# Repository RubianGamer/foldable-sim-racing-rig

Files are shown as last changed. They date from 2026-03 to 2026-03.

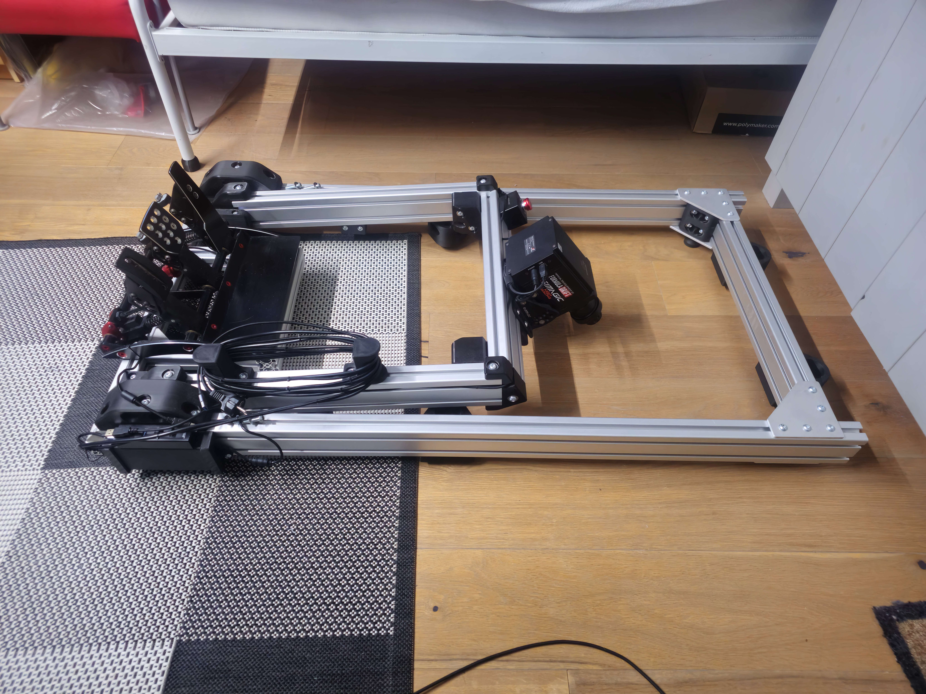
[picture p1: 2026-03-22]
images/20250122_214839.jpg

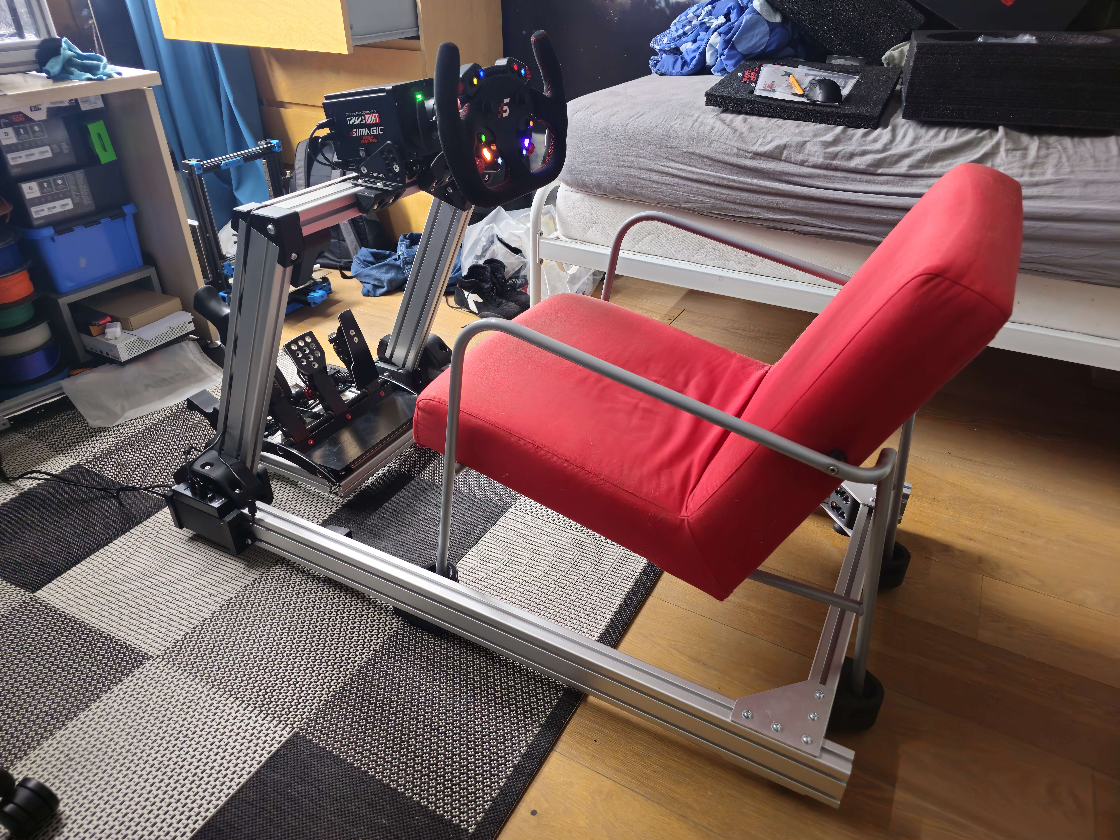
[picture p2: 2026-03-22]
images/20240603_111210.jpg

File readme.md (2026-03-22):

due to popular demand, here are the files for my folding sim rig/wheel stand.

was made to fit me (180cm tall, avg/slender build) with a random thrift shop seat set down in some mounts, so you will need to design your own seat mount or figure out what seat i used and find one somewhere lol (its a great chair)

my hardware is a simagic alpha mini with fanatec clubsport V3 pedals. the wheeldeck can prob support most deck mounted wheelbases, but the pedal deck is made specifically for the clubsport V3 pedals, so you might have to make something yourself if you use different pedal.

file comes with side braces, but after building it, i found out the deck as is can support my full weight (70kg) with practically no deflection even when moving around, so are not really needed.

some of the hardware might be difficult to source locally, especially the large washers and sholder bolts, but aliexpress has pretty much all of the hardware required. i got the brackets/plates/profiles off of aluxprofiel locally.

for the sholder bolts, the sholder is M12 (so 12mm), and the threads will be M10.

for the printed parts, print all the parts out of PLA/ASA with 3.2mm shell (8 perimiters and 16 top/bottom layers on .4 nozzle .2 layer height) and 50% infill for proper strenght, avoid PETG and ABS due to the material being less stiff. if you want absolutely no flex out of the printed parts you can always print with filled filaments, or with CF-PPS if you hate your wallet :)

render_front

render_front

render_front

render_front

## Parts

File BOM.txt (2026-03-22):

the parts you will need for the build. 

extrusion sizes:
490mm 8040  1x (wheel deck)
585mm 8040 2x (wheel deck stand)
700mm 4040 1x (front main frame)
1285mm 8040 2x (main frame sides)
620mm 8040 1x (rear main frame

only for fanatec clubsport V3 pedals:
208mm 4040 2x
325mm 4040 1x

screws:
M5x12 BHCS
M5x7mm heatset insert (8x) (9,5mm max lenght)

M8x60 BHCS
M8x30 BHCS
M8x20 BHCS
M8x16 BHCS
M8 hex nut
M8x20mm washer
M8 roll in nut for 40 series profile
rubber feet with M8 thread (see cad)

M12xx70mm sholder bolts (2x)
M12x25mm washer (2x)

M10 hex nut (2x)
M10x25x1,5mm washer (2x)

(ID,OD,lenght)
12x18x20 bronze bushing (6x)
12x18x12 bronze bushing (2x)

brackets:
4x 40 series L profile corner plates (2 need 10mm hole drilled)
2x square plate (4x2 holes, 40x80mm spacing, see cad)
4x 90 deg 40 series corner bracket (4x more for fanatec clubsport V3 pedal frame)

only for side braces:
245mm 4040 2x
M5x40 BHCS (8x)
M5 hex nut (8x)
M12x35mm sholder bolt (4x)
M10 hex nut (4x)
M10x25x1,5mm washer (4x)
M5x7mm heatset insert (16x) (9,5mm max lenght)

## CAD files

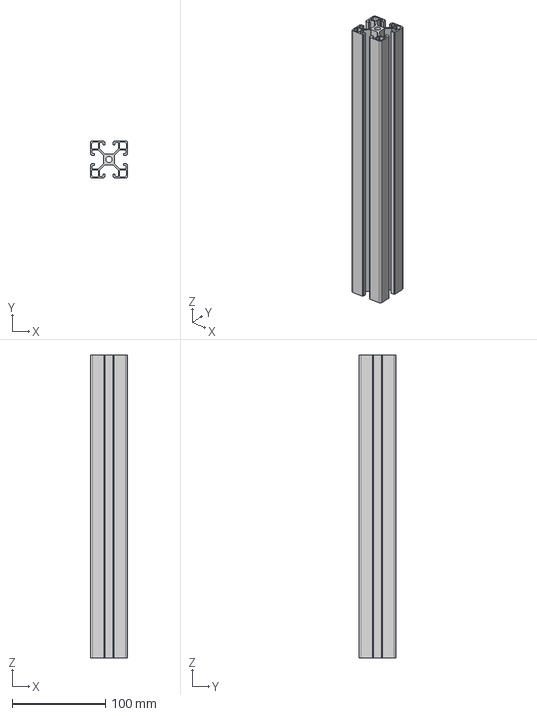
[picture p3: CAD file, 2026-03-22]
design files/step/aluminum profiles/fwd pedal mount v1.step
40.0 x 40.0 x 325.0 mm

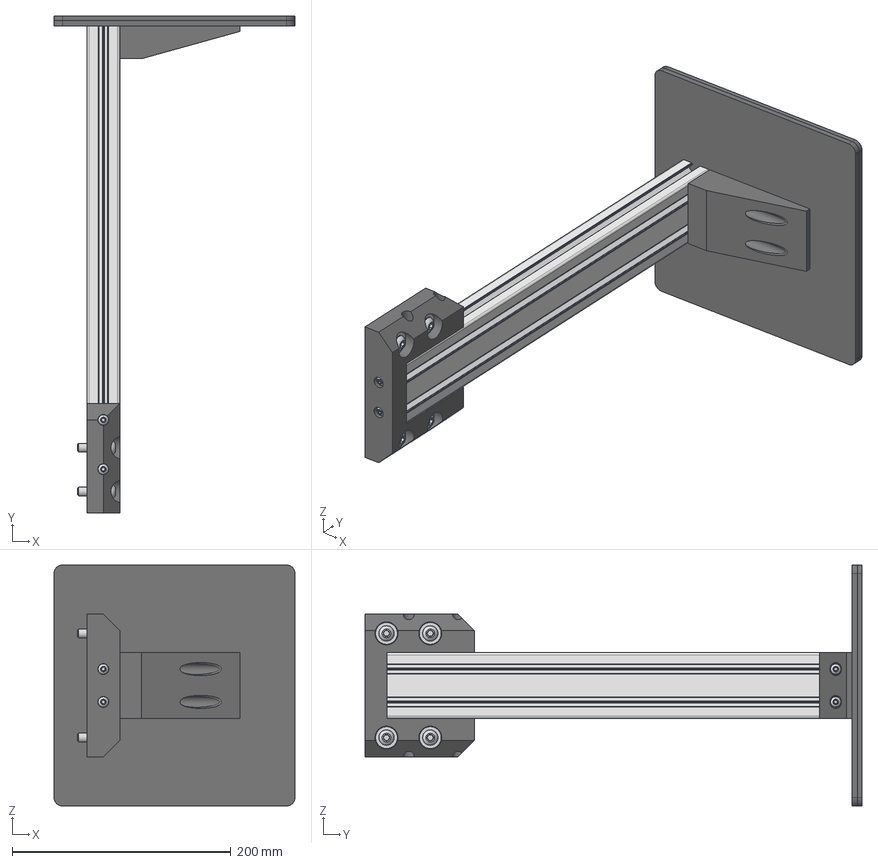
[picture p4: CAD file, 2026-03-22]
design files/step/assamblies/mouse pad stand v1.step
220.0 x 454.0 x 220.0 mm
3060 bottom frame
mousepad stand mount_1
M5x25 BHCS_1 x 4
M5x12 BHCS_1 x 4
mouse pad base_1
mouse pad ridge
M8x20 washer_1 x 4
92095A290_NO THREADS x 4

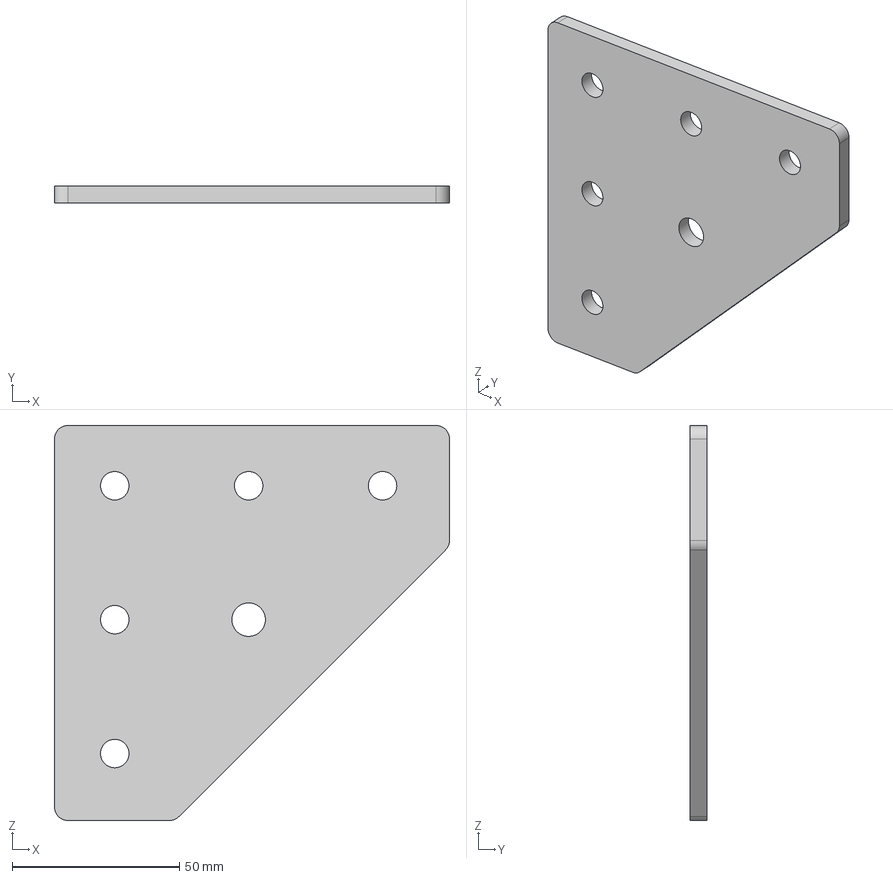
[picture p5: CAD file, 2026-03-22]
design files/step/hardware/brackets/lwr L corner bracket v3.step
118.0 x 5.00 x 118.0 mm

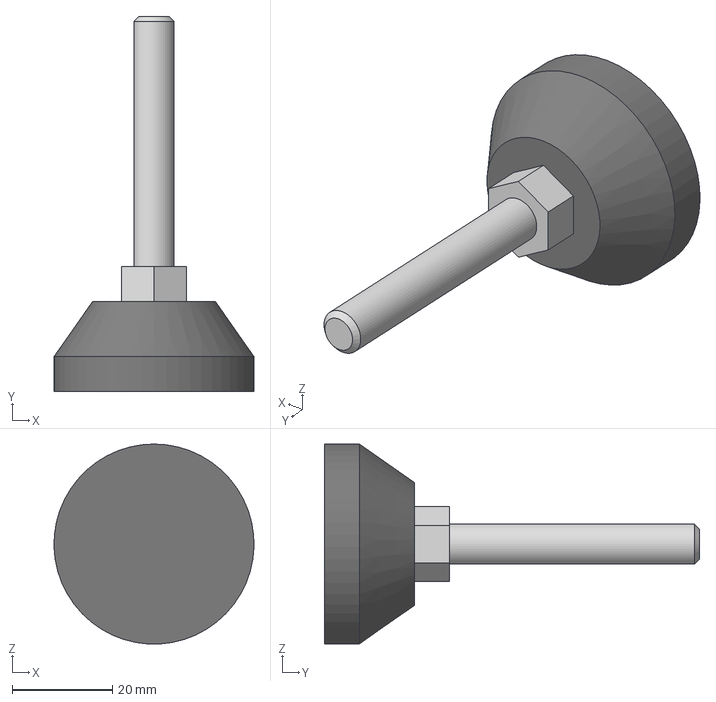
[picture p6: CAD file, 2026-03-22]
design files/step/hardware/misc/rubber feet v1.step
40.0 x 75.0 x 40.0 mm

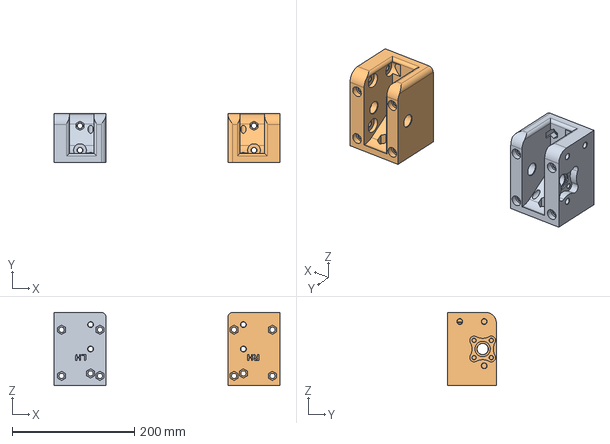
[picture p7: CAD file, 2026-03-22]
design files/step/printed parts/wheel stand mount v15.step
370.4 x 80.0 x 120.0 mm
wheel stand mount LH
wheel stand mount RH

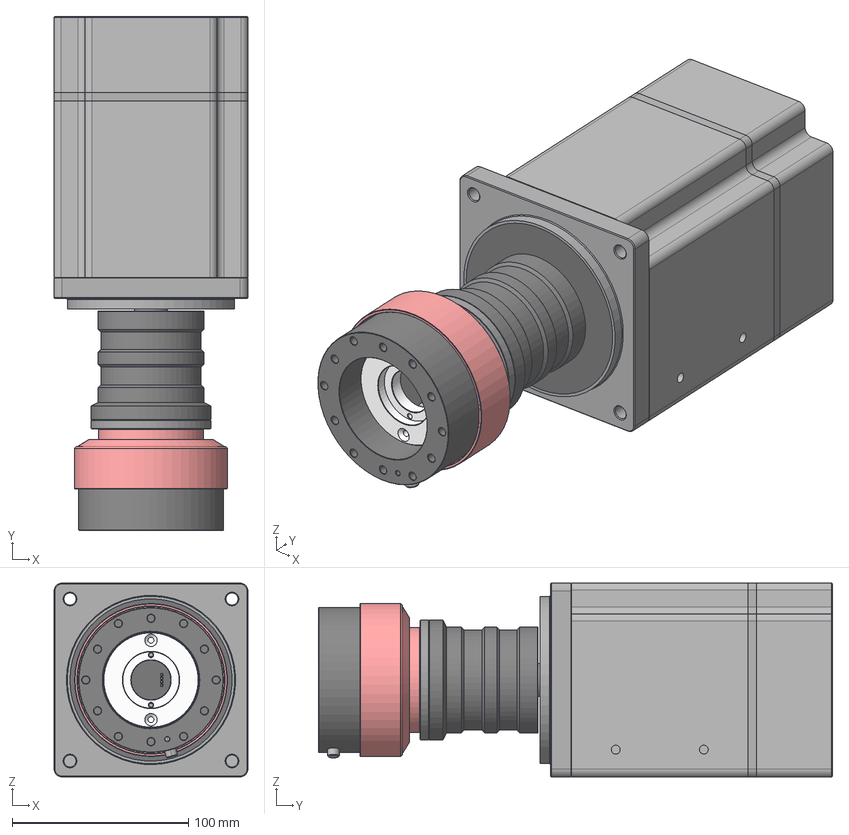
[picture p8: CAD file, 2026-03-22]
design files/step/sim stuff/Simagic Alpha Mini w QR v1.step
110.0 x 291.7 x 110.0 mm
PCB
Inner
Outer
Inner PCB Mount
M3x4 v1
M3x4 v1 (1)
Base Side
Front Mount Plate
Main Casing
Rear Plate
PCB Casing
CF Cover
Shaft 19mm
Shaft Clamp

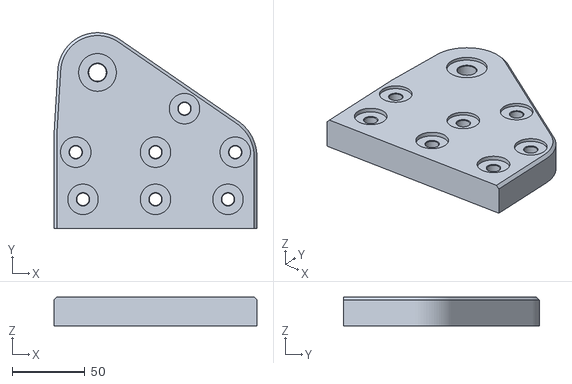
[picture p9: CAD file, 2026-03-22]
printed parts/optional/side brace/side brace base LH outboard.stl
140.0 x 134.9 x 20.0

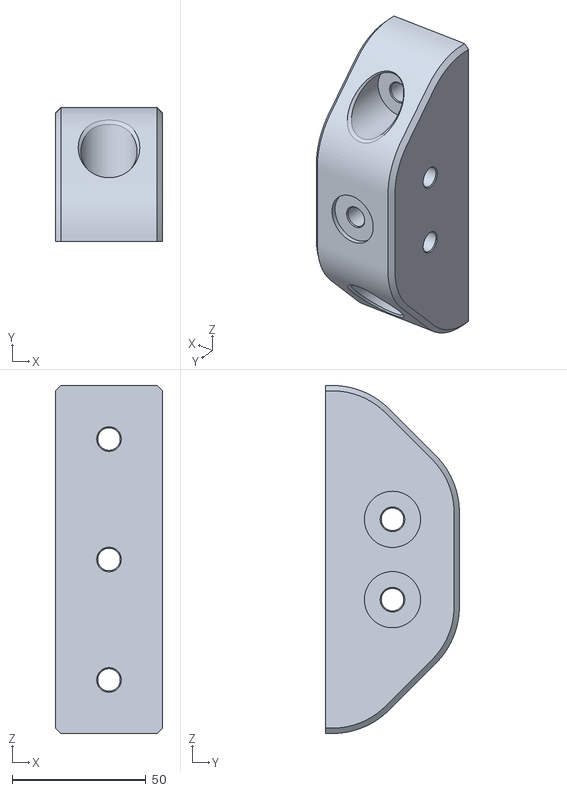
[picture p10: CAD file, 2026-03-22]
printed parts/optional/simagic DS-8X shifter/stifter stand top mount.stl
40.0 x 50.0 x 130.0

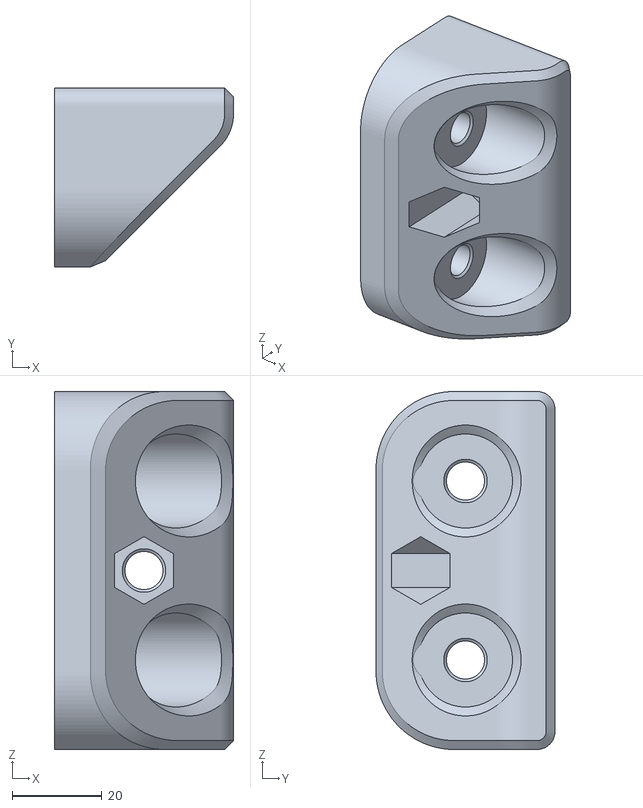
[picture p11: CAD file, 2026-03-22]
printed parts/optional/wheel mount spacer (optional).stl
40.0 x 40.0 x 80.0

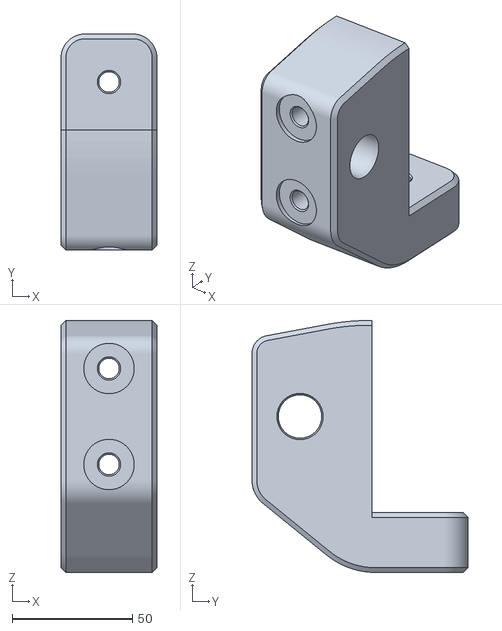
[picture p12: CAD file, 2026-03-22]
printed parts/wheel stand hinge point 2x.stl
40.0 x 90.0 x 105.0

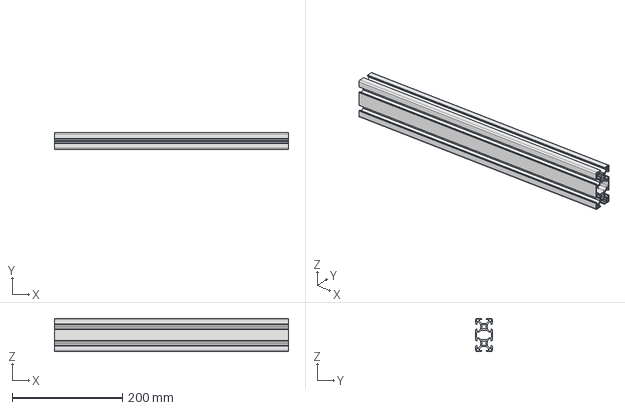
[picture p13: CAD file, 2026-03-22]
design files/step/aluminum profiles/mouse deck v1.step
425.0 x 30.0 x 60.0 mm

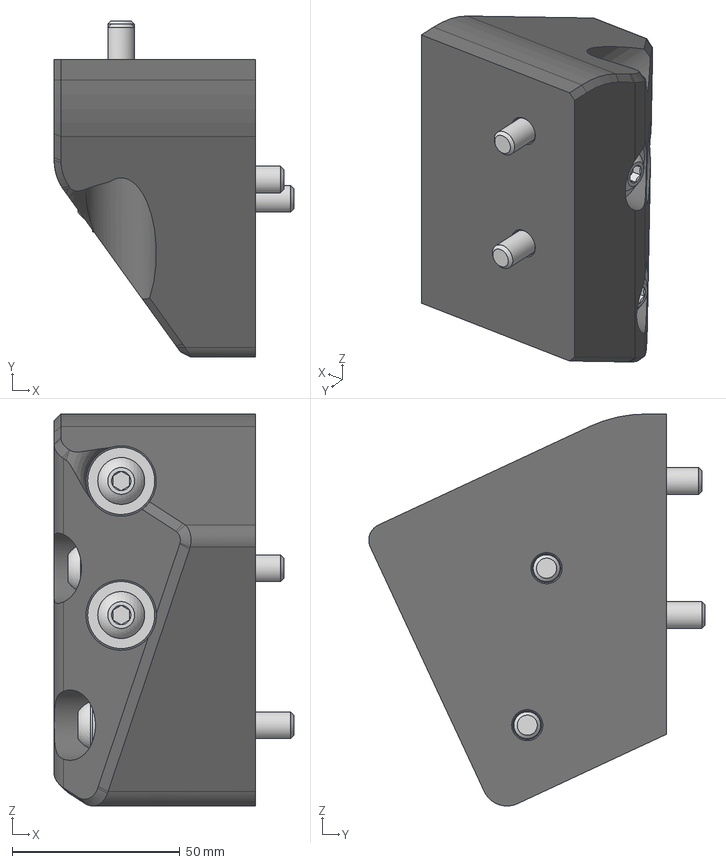
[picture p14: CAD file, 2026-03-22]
design files/step/assamblies/deck mount RH v4.step
71.5 x 100.4 x 116.9 mm
M8x20 washer_3 x 4
92095A290_NO THREADS
M8x60 BHCS_2 x 3
deck mount RH_1

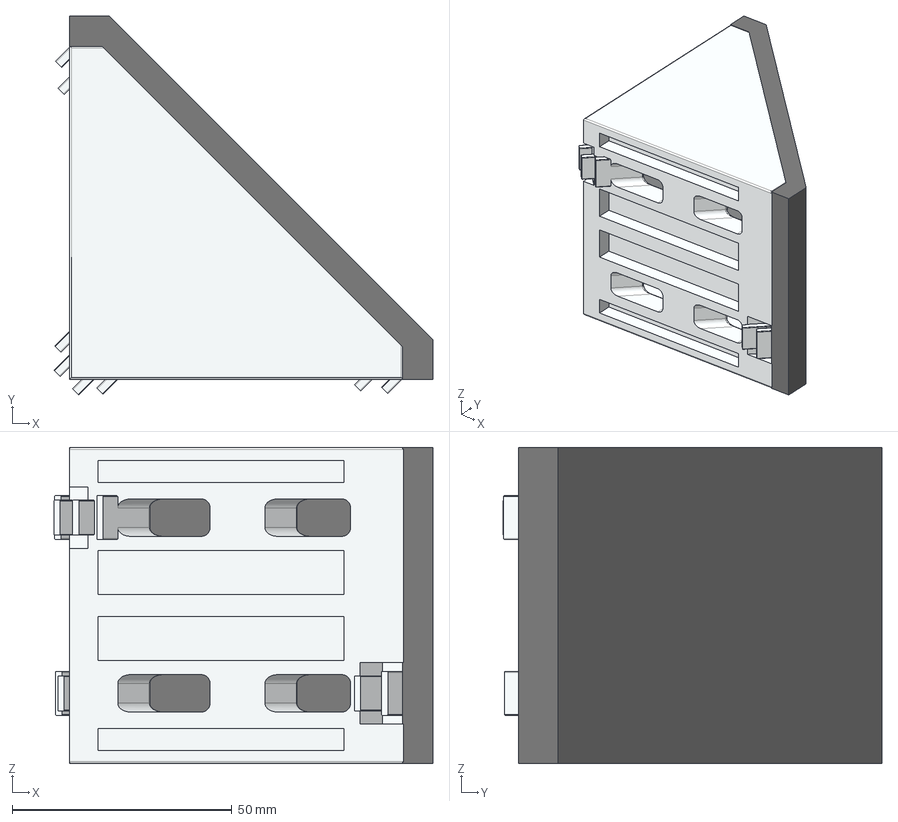
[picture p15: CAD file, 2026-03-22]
design files/step/hardware/brackets/8080 corner bracket v1.step
86.3 x 86.3 x 72.0 mm
8080L+Cover
8080L Cover

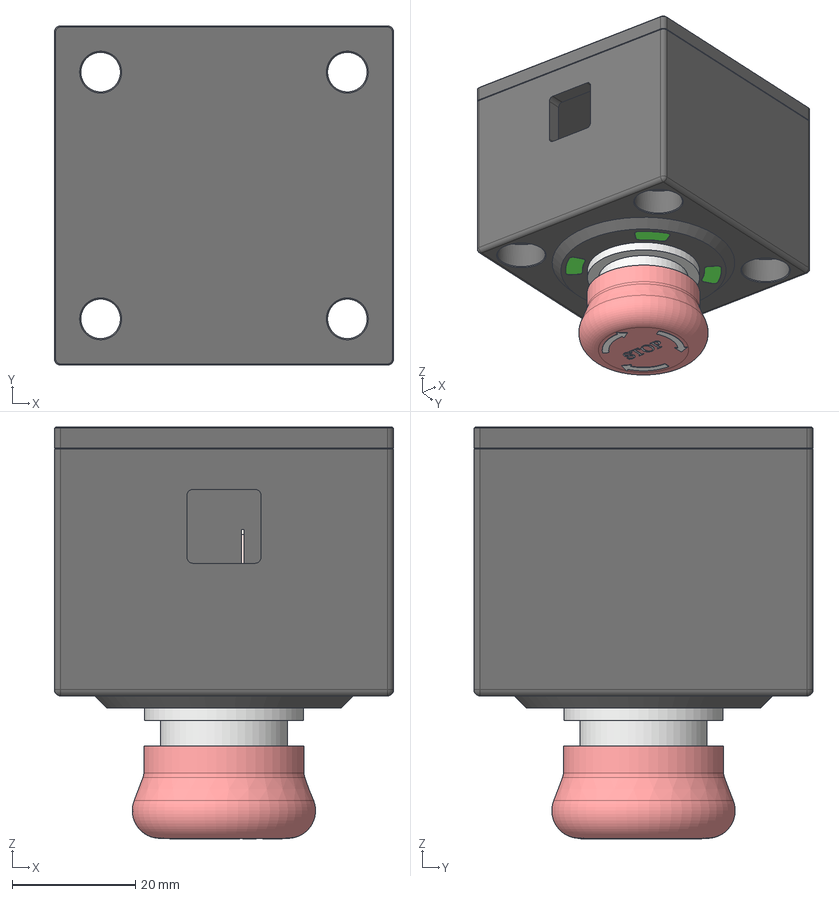
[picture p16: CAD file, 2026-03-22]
design files/step/sim stuff/Simagic Emergency switch v2 v1.step
55.0 x 55.0 x 66.8 mm
Main Housing
Base Cap
LED1
LED2
LED3
LED4
Switch (1)
Terminal 1
Terminal 2
Terminal 3
Terminal Base connection
Base
Actuator
Main Body
Nut
O-ring
Button Cap

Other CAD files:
design files/step/printed parts/wheel mount spacer v1.step
printed parts/optional/aft chair mount 2x.stl
design files/step/aluminum profiles/pedal mount v1.step
design files/step/assamblies/wheel stand rigid mount v4.step
design files/fusion/assamblies/L corner bracket v1.f3z
design files/fusion/assamblies/aft feet v6.f3z
design files/fusion/assamblies/aft pedal crossbrace v1.f3d
design files/fusion/assamblies/base crossbrace v3.f3d
design files/fusion/assamblies/base side v3.f3d
design files/fusion/assamblies/deck mount LH v4.f3z
design files/fusion/assamblies/fwd pedal mount v1.f3d
design files/fusion/assamblies/mouse deck v1.f3d
design files/fusion/assamblies/mouse pad stand v1.f3z
design files/fusion/assamblies/pedal brace v1.f3d
design files/fusion/assamblies/pedal crossbrace v1.f3d
design files/fusion/assamblies/pedal mount v1.f3d
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
